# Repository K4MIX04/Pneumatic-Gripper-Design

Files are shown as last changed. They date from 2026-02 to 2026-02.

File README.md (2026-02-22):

# Pneumatic Gripper Design (University Project)

This repository contains an academic project completed as part of my Automation and Robotics degree at AGH University of Science and Technology.

## Project Overview
The goal of the assignment was to design a functional pneumatic gripper capable of lifting a specific payload, starting from basic kinematic equations up to a complete 3D assembly and technical documentation.

### Key phases of the project:
* **Kinematic & Force Analysis:** Mathematical calculations and simulations (using SAM) to determine the required gripping forces and stroke lengths.
* **Component Selection:** Sizing and selecting an appropriate pneumatic cylinder from the industrial **Festo** catalog.
* **CAD Modeling & FEA:** 3D parametric modeling and stress analysis (von Mises) performed in **Autodesk Inventor** to verify structural integrity.
* **Technical Documentation:** Creation of 2D assembly drawings and a complete Bill of Materials (BOM).

---

### Project Gallery

**
**Fig 1.** 3D Render of the designed gripper.

**
**Fig 2.** Finite Element Analysis (FEA) / von Mises stress test in Autodesk Inventor.

**
**
**Fig 3.** 2D Assembly Drawing.

---
*Note: This is strictly an educational project created for university coursework. Full documentation (in Polish) is available in the attached PDF file.*

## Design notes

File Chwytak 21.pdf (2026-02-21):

1

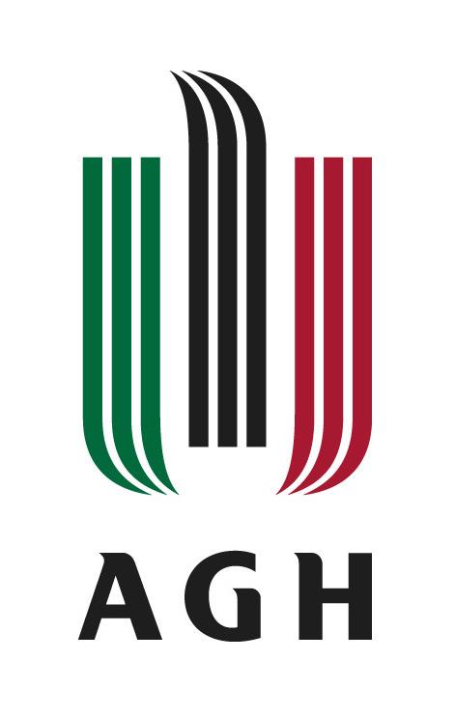
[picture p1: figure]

Projekt konstrukcyjny chwytaka nr 21 typu P – (O – P – Os)

## Projekt konstrukcyjny chwytaka nr 21 typu P – (O – P – Os)

Prototypowanie konstrukcji w technice druku 3D i CNC

## Kamil Górak

## Automatyka i Robotyka Wydział Elektrotechniki, Automatyki, Informatyki i Inżynierii Biomedycznej

2

## Spis treści

1. Założenia wykonywanego projektu | 3
2. Schemat chwytaka przemysłowego | 3
3. Obliczenia ruchliwości zadanego chwytaka | 3
4. Wyznaczenie maksymalnej siły ciężkości wałka | 4
5. Wyznaczanie potrzebnej siły chwytu | 4
6. Wyznaczenie minimalnej długości szczęk | 5
7. Wyznaczenie długości poszczególnych elementów chwytaka | 5
8. Charakterystyka przesunięciowa | 7
9. Charakterystyka prędkościowa | 10
10. Charakterystyka siłowa | 11
11. Wytrzymałość na ścinanie dla sworznia | 14
12. Analiza wytrzymałościowa w programie Autodesk Inventor | 15
13. Dobór siłownika | 16
14. Rysunek złożeniowy chwytaka | 17
15. Źródła | 20

3

## 1. Założenia wykonywanego projektu

- Obiektem przeznaczonym do przeniesienia jest wałek o średnicy zewnętrznej wynoszącej 80 mm, długości 140 mm, wykonany ze stopu aluminium
- Urządzenie ma za zadanie chwycić transportowany element, utrzymać go podczas transportu i uwolnić w miejscu docelowym
- Siłownik chwytaka jest zasilany sprężonym powietrzem o ciśnieniu 0,6 MPa

## 2. Schemat chwytaka przemysłowego

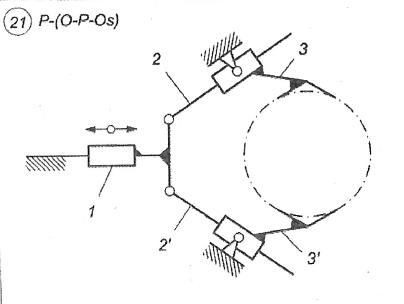
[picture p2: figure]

## 3. Obliczanie ruchliwości zadanego chwytaka

Aby wyznaczyć ile elementów jest potrzebne do napędu projektowanego urządzenia posługuję się następującym wzorem:
W = 3n - ∑ ( i − 3)

5
i=3 | pin
Który po przekształceniu do obecnych warunków zadania przyjmuje postać: W = 3n – p4 - 2p5
Gdzie:
W – ruchliwość chwytaka
n – liczba członów ruchomych
p4 – liczba par kinematycznych klasy czwartej p5 – liczba par kinematycznych klasy piątej

4

Po podstawieniu wartości:
n = 5
p4 = 0
p5 = 7
W = 3*5 – 0 – 2*7 = 1

Z faktu, że W = 1 wynika, że do napędu chwytaka wymagany jest jeden siłownik o ruchu liniowym

## 4. Wyznaczanie maksymalnej siły ciężkości wałka

Maksymalny ciężar transportowanego elementu uzyskuję ze wzoru:
Qmax = πr
2

lρg
Gdzie:
r = 40 mm promień wałka
l = 140 mm długość wałka
ρ = 2700 kg m3 | przyjęta gęstość aluminium
| Qmax = 3,1415 * (0,04m)² * 0,14m * 9,81m
s2

* 2700 kg
m3
Qmax = 18,64N

## 5. Wyznaczanie potrzebnej siły chwytu

Ustalenie wymaganej siły chwytu przebiega na podstawie analizy poniższego schematu przedstawiającego szczęki zaciśnięte na przedmiocie

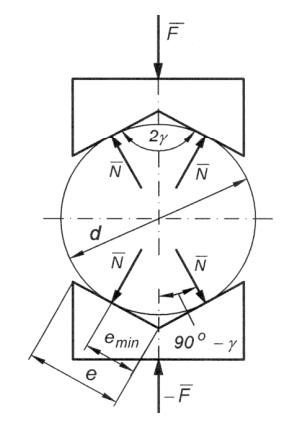
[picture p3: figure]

5

Przyjmujemy następujące wartości: μ = 0,3
2γ = 125o
n = 2
Qmax = 18,64 N
Na podstawie powyższego schematu oraz podanych wartości przystępujemy do wyznaczenia potrzebnej siły chwytu
Fch = 2 N cos(90o – γ) | → | N = Fcℎ
2sinγ
T = μ n | → | T = μFch
2sinγ
Aby udało się chwycić wałek musi być spełniony następujący warunek
4T ≥ Qn | → | Fch ≥

nQmaxsinγ
2μ
Podstawiając wartości liczbowe otrzymuję
Fch ≥ 82,67N

## 6. Wyznaczenie minimalnej długości szczęk

Korzystając ze schematu przedstawionego w poprzednim punkcie przystępuję do wyznaczenia długości szczęk korzystając z zależności:
tg γ =

0,5d
emin

→ emin =

d
2tgγ

≈ 21 mm
Aby mieć pewność, że wyznaczona długość będzie wystarczająca przyjmuję e z określonego zakresu
e = (1,1 – 1,5) emin
W związku z powyższym w moim przypadku e = 30 mm

## 7. Wyznaczenie długości poszczególnych elementów chwytaka

Aby wyznaczyć odpowiednie długości poszczególnych części chwytaka a także kątów między nimi użyłem programu Autodesk Inventor. Zaprojektowałem w nim schemat kinematyczny wykonywanego manipulatora uzyskany poprzez łączenie odpowiednich ramion wiązaniami, ustalanie stałych długości. Wykonywane czynności tj. zmiana poszczególnych wartości pozwoliły mi wyznaczyć wymiary, przy których chwytak pracował w zadowalający sposób. Używany schemat a także wyznaczone z niego długości, które będą wykorzystywane w dalszym ciągu obliczeń umieściłem poniżej.

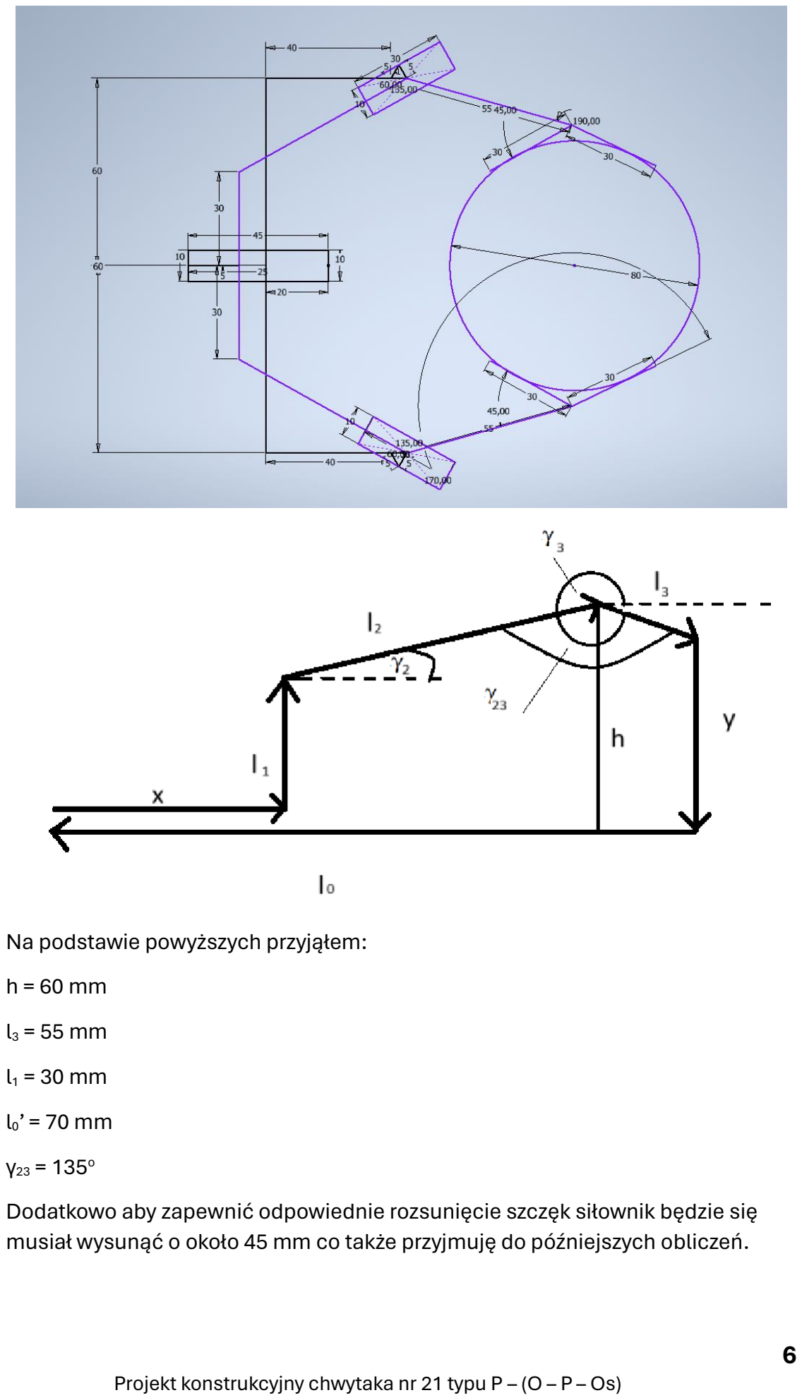
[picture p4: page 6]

6

Na podstawie powyższych przyjąłem: h = 60 mm
l3 = 55 mm
l1 = 30 mm
l0’ = 70 mm
γ23 = 135o
Dodatkowo aby zapewnić odpowiednie rozsunięcie szczęk siłownik będzie się musiał wysunąć o około 45 mm co także przyjmuję do późniejszych obliczeń.

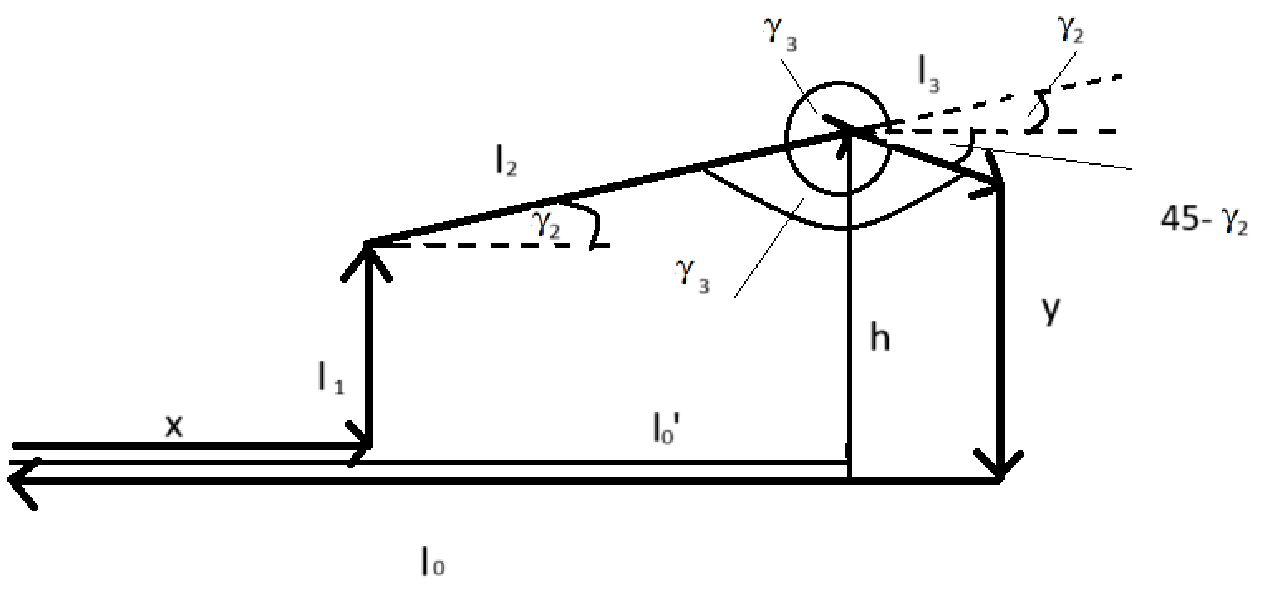
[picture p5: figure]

7

## 8. Charakterystyka przesunięciowa

Aby wyznaczyć funkcję położenia szczęki w zależności od wysunięcia tłoka posługuję się schematem z powyższego punktu uzupełnionym o dodatkową odległość i kąty.

Korzystając z metody wieloboku wektorowego zamkniętego przystępuję do wyznaczania charakterystyki przesunięciowej.

Zapisuję równania wektorowe dla dwóch wieloboków, które mogę wyróżnić
x̅+ l̅1 + l̅2 + l̅3 + y̅ + l̅0 = 0 x̅+ l̅1 + l̅2 + ℎ̅ + l′0

̅̅ = 0

Następnie zapisuję równania dla obu osi dla wieloboku mniejszego x + l2cos γ2 - l0’ = 0
l1 + l2sin γ2 - h = 0
l0’ – x = l2cos γ2
h – l = l2cos γ2
(l0’ – x)² = l2

2cos² γ2
(h – l1)

2 = l2

2sin² γ2
(l0’ – x)² + (h – l1)

2 = l2
2

(cos² γ2 + sin² γ2)
l2 = √(l0’ – x)
2 + (h – l1)

2
cos γ2 =

l

′0−x

l2

=

l

′0−x
√(l0’ – x)² + (h – l1)²
sin γ2 =

ℎ−l1
l2

=

ℎ−l1
√(l0’ – x)² + (h – l1)²

Dodatkowo zauważam, że
γ3 = 315o + γ2

8

Wyznaczone z małego wieloboku dane używam do rozwiązania układu większego wieloboku.
x + l2cos γ2 + l3cos γ3 - l0 = 0 l1 + l2sin γ2 + l3sin γ3 - y = 0 x + l1 + l2(

l

′0−x

l2

+

ℎ−l1
l2

) + l3(cos γ3 + sin γ3) – l0 - y = 0 h + l’0 + l3(cos γ3 + sin γ3) – l0 – y = 0

Dodaję kolejne równanie odczytane ze schematu: l0 = l’0 + l3cos(45o

- γ2)
Wracając do wcześniejszego równania:
h + l’0 + l3(cos(315o + γ2) + sin (315o + γ2)) -l3cos(45o
- γ2) – y – l’0 = 0

h + l3[(√2
2

l

′0−x
√(l0’ – x)² + (h – l1)² +

√2
2

ℎ−l1
√(l0’ – x)² + (h – l1)²

) + (−

√2
2

l

′0−x
√(l0’ – x)² + (h – l1)² +

√2
2

ℎ−l1
√(l0’ – x)² + (h – l1)²

) - (

√2
2

l

′0−x
√(l0’ – x)² + (h – l1)² +

√2
2

ℎ−l1
√(l0’ – x)² + (h – l1)²

)] = y

Po uproszczeniu dochodzę do równania y = h + l3

√2
2

(

x+ℎ−l1−l′0
√(l0’ – x)² + (h – l1)²

)

Po podstawieniu wartości liczbowych otrzymuję charakterystykę przesunięciową: y = 60 + 27,5√2 (

x−40
√(70−x)2+900

)

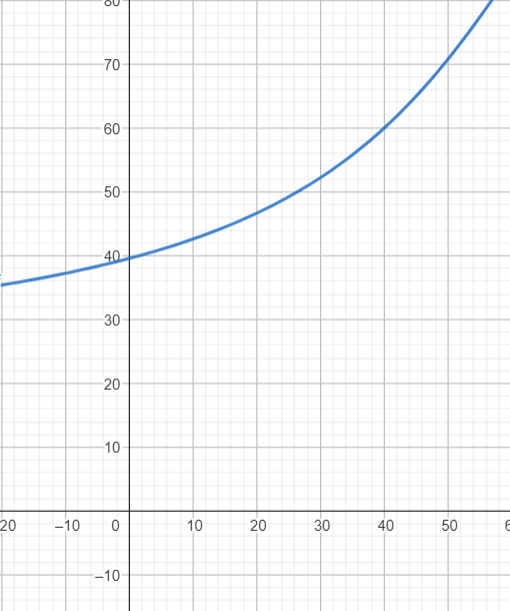
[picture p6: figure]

Przedstawiony powyżej wykres został wygenerowany przez stronę geogebra.org i przedstawia wykres charakterystyki według wyznaczonego równania. Uzyskana

9

charakterystyka jest zgodna ze schematem wykonanym w Autodesk Inventor tzn. wysunięcie tłoka o daną długość i zmiana wysokości y są zgodne ze sobą. Aby jeszcze dokładniej przekonać się o poprawności wyznaczonej charakterystyki zamodelowałem schemat chwytaka w programie SAM 8.3, który zamieściłem poniżej.

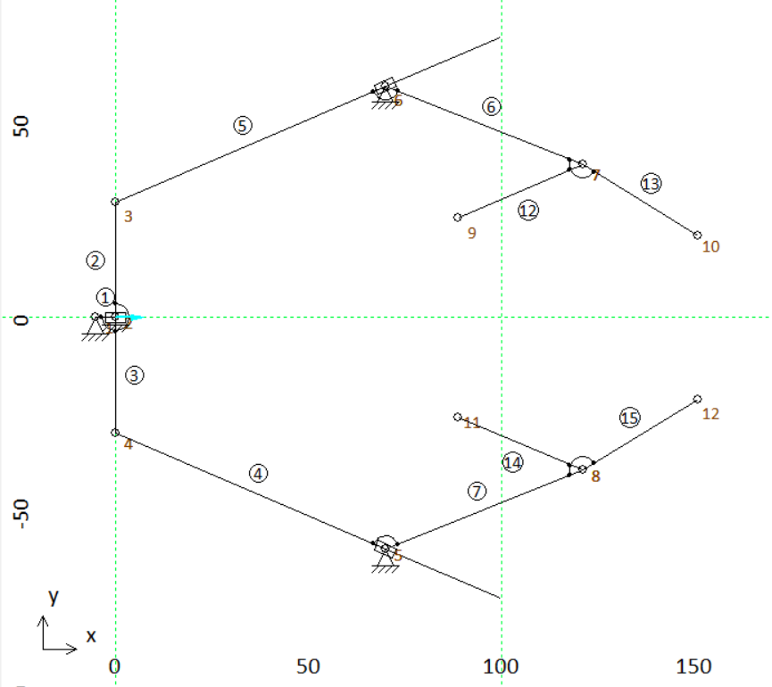
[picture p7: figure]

Wykorzystując wbudowaną w program funkcję do generowania wybranych wykresów otrzymałem następującą charakterystykę przesunięciową.

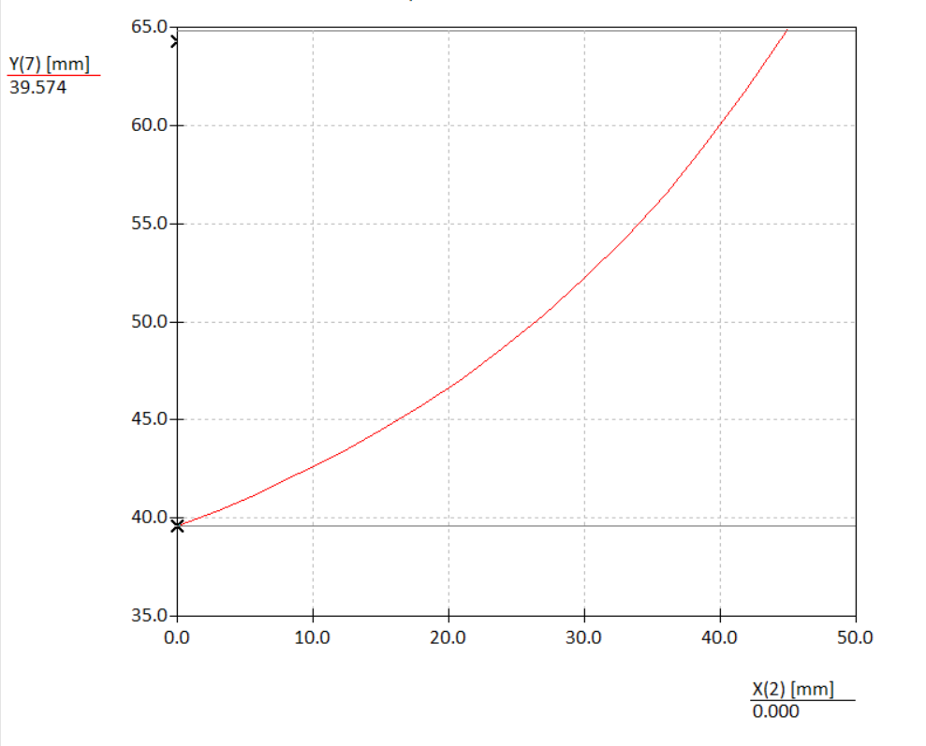
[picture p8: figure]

Powyższy wykres dokładnie nakłada się na wykres uzyskany z własnoręcznych obliczeń.

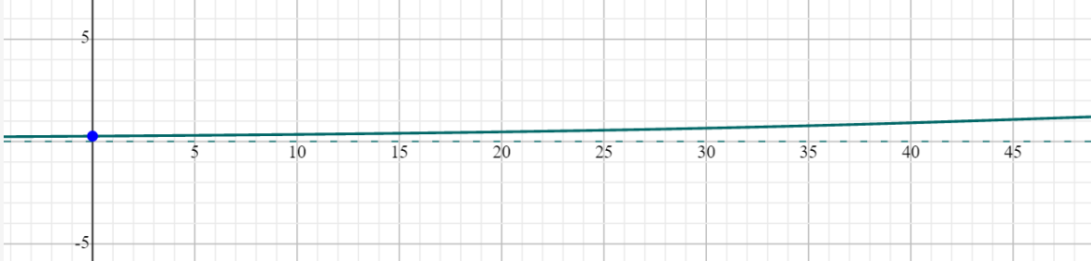
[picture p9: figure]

10

## 9. Charakterystyka prędkościowa

Charakterystykę prędkościową wyliczam metodą analityczną licząc pochodną y(x) po zmiennej x.

d
dx

y =

d
dx

(60 + 27,5√2 (

x−40
√(70−x)²+900

))

Otrzymuję:

fv (x) = | −825√2x+82500√2

x

| 2∗√(70−x)2+900−140x√(70−x)2+900+5800√(70−x)2+900
Generuję wykres z użyciem programu symbolab.com

Sprawdzam czy otrzymałem dobrą charakterystyką porównując otrzymany powyżej wykres z wygenerowanym przez program SAM

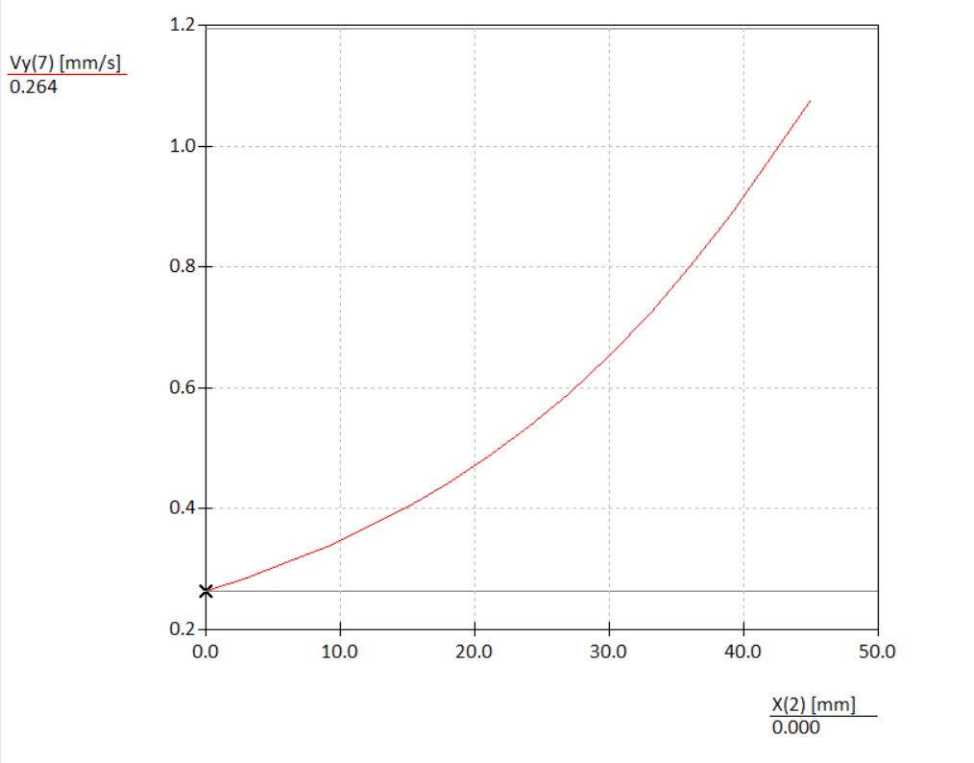
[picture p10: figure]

Porównując wybrane wartości mogę stwierdzić, że wykresy te są ze sobą zgodne.

11

## 10. Charakterystyka siłowa

Pierwszym sposobem wyznaczenia charakterystyki siłowej jest metoda analityczna, która polega na rozpatrywaniu sił działających na poszczególne części członów.
a) Człon 1

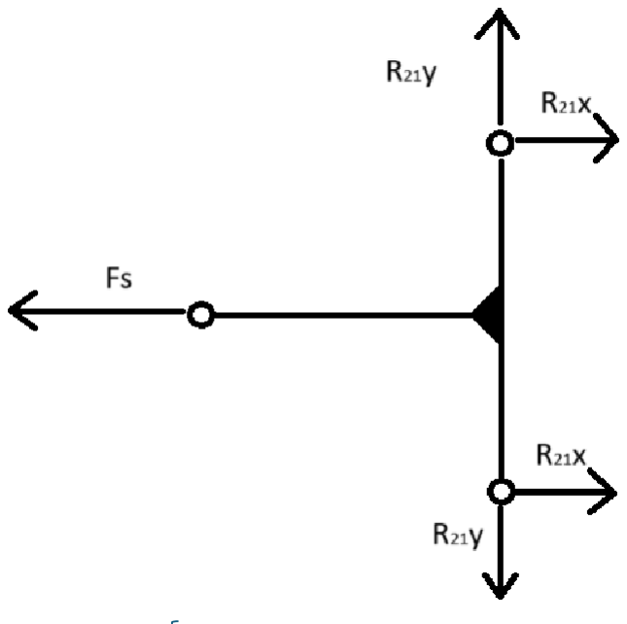
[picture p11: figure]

-FS + 2R21

x = 0
FS = 2R21
x
b) Człon 2

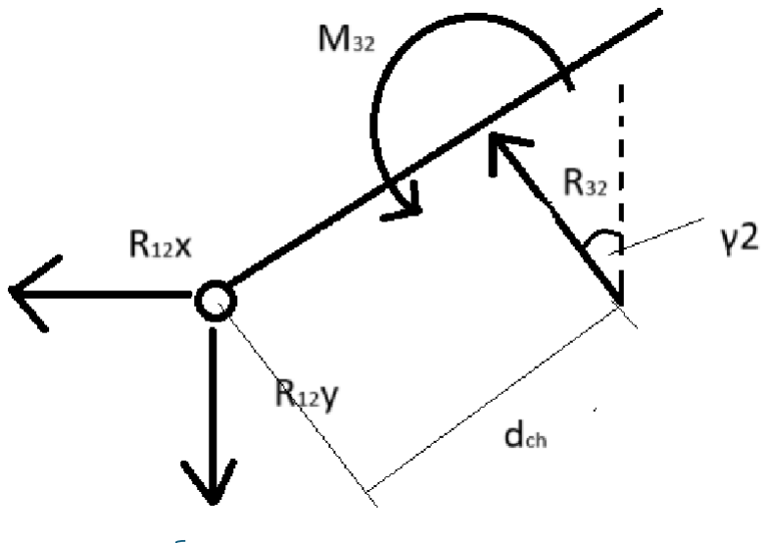
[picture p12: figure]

- R12

X – R32*sin γ2 = 0
- R12

y + R32*cos γ2 = 0
M32 – R32*dch = 0
c) Człon 3

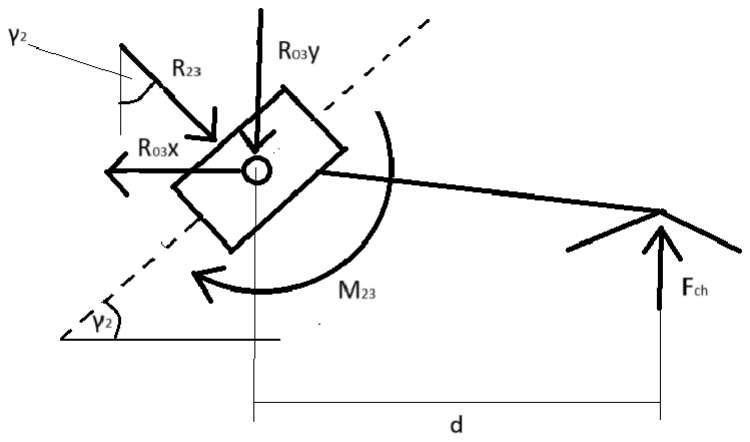
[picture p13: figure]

12

- R03

X + R23*sin γ2 = 0
-R03

Y – R23cos γ2 + Fch = 0
- M23 + Fch*d = 0

Podsumowując wszystkie otrzymane równanie otrzymujemy:
- FS + 2R21

x = 0
FS = 2R21
x
- R12

X – R32*sin γ2 = 0
- R12

y + R32*cos γ2 = 0
M32 – R32*dch = 0
- R03

X + R23*sin γ2 = 0
-R03

Y – R23cos γ2 + Fch = 0
- M23 + Fch*d = 0
Wykorzystując znane wartości: γ2 = 29,2o
d = 52,923 mm
dch = 61,483 mm
Fch = 82,67 N
Otrzymujemy równania, z których wyznaczamy kolejno: M23 = Fch * d
M23 = 82,67 N * 0,052923 m = 4,375 Nm R32 =

M32
dcℎ

= 71,158 N

R12

y = R32cos γ2 = 62,115 N

R12

x = - R32sin γ2 = - 34,715 N

Fs = 2R21

x = 69,43 N
Wyznaczona powyżej siła to minimalna siła jaką musi posiadać siłownik aby zacisnąć szczęki z minimalną wymaganą siłą, tak aby wałek się nie wyślizgnął.

Aby sprawdzić poprawność wyznaczonej siły skorzystam z metody mocy chwilowych. Korzystając ze wzoru:
Fcℎ
Fs =

1
2fv(x)

Który po przekształceniu i podstawieniu wartości przyjmuje postać:

2 ∗

−825√2x + 82500√2

x

2 ∗ √(70 − x)

2 + 900 − 140x√(70 − x)

2 + 900 + 5800√(70 − x)
2 + 900

∗ 82,67

Korzystając z Geogebry generuję wykres powyższej funkcji

13

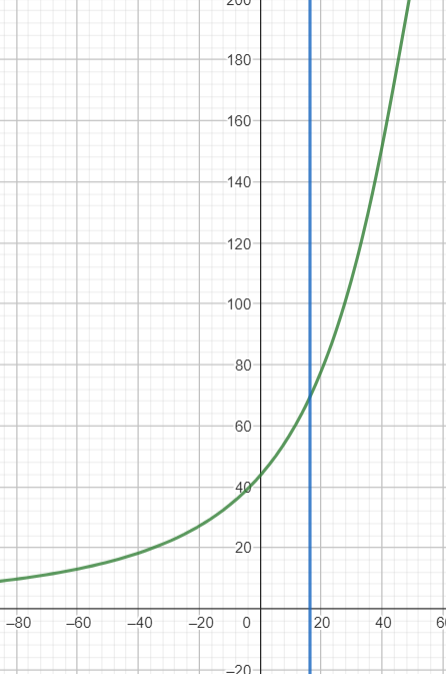
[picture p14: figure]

Aby się upewnić skorzystałem również z opcji oferowanych przez program SAM, który po przyłożeniu siły w sposób przedstawiony poniżej pozwala wygenerować wykres siły potrzebnej na tłoku.

Zielonym kolorem został
oznaczony szukany wykres a pionowa niebieska kreska
symbolizuje punkt, w którym szczęki zaciskają się na wałku. Siła w tym miejscu wynosi w
zaokrągleniu 70 N co zgadza się z wyznaczeniem metodą
analityczną

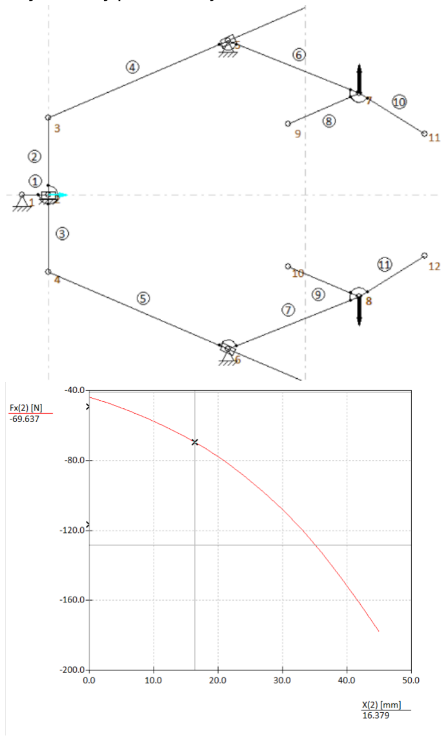
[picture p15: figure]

14

Zaznaczony punkt symbolizuje miejsce, w którym szczęki się zaciskają co po raz kolejny potwierdza poprawność wykonanych obliczeń.

## 11. Wytrzymałość na ścinanie dla sworznia

Po analizie schematu chwytaka stwierdzam, że największym obciążeniom będzie podlegał sworzeń znajdujący się na belce, do której przymocowany jest tłok, gdyż będzie on pojedynczy w przeciwieństwie do sworznia mocującego ramę ze szczękami, który będzie łączony za pomocą dwóch sworzni z każdej strony jeden.

Warunek wytrzymałości sworznia na ścinanie jest wyrażony zależnością:
στ≤ kτ, gdzie
kτ – dopuszczalne naprężenie ścinające
στ – maksymalne naprężenie ścinające

kτ = 132 MPa (odczytane z dostępnych źródeł)

στ =

2T
π∗d²
d – średnica sworznia (przyjęta) = 6 mm
T – siła tnąca
Korzystając z przeprowadzonej wcześniej analizy siłowej mogę obliczyć siłę ścinającą działającą na wybrany sworzeń. (Punkt 10, podpunkt b)

T = √(R03y)
2 + (R03x)

2

T = √(62,115N)
2 + (34,715N)

2
T = 71,16 N
Co podstawiam do wyżej zapisanych wzorów i otrzymuję:

στ =

2∗71,16N
3,1415∗(0,006m)²

= 1,26 MPa

Otrzymane wyniki prowadzą do stwierdzenia, że sworzeń wytrzyma działanie na niego sił ścinających.

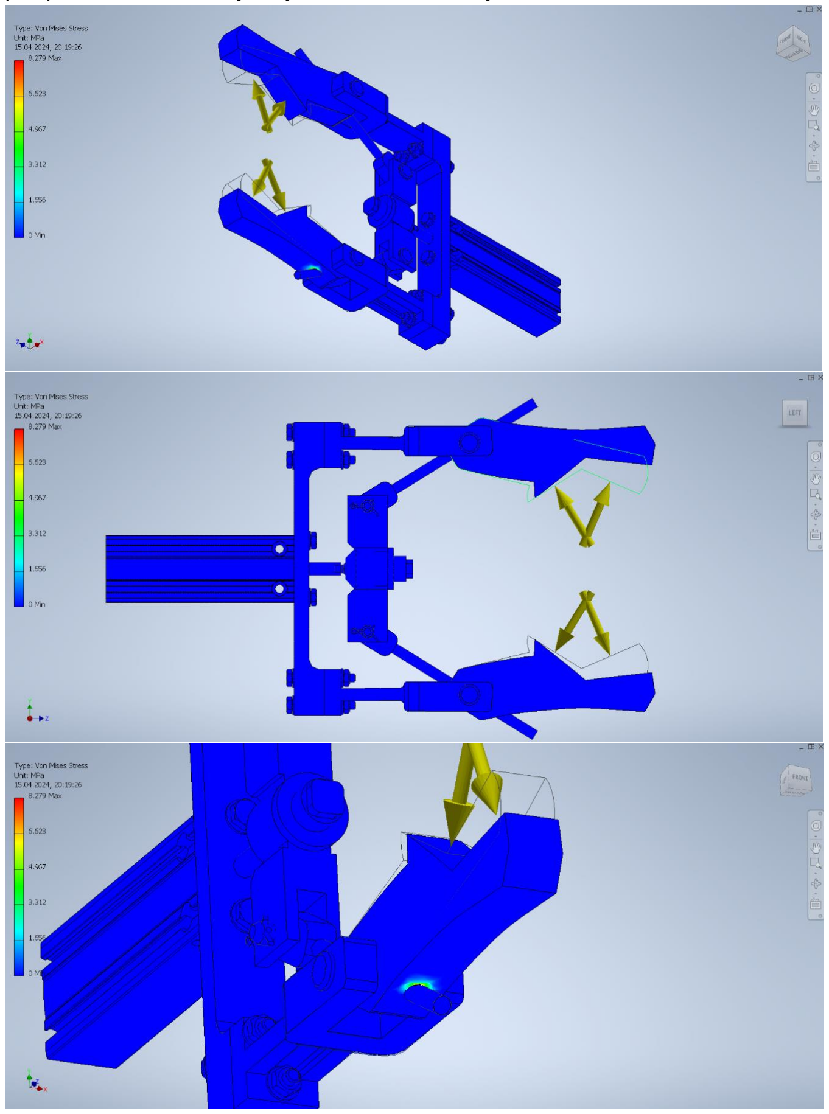
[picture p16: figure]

15

## 12. Analiza wytrzymałościowa w programie Autodesk Inventor

Aby sprawdzić czy chwytak wytrzyma poddawane mu obciążenia i działające siły przeprowadziłem analizę z użyciem modułu Analizy w Inventorze.

Wyniki potwierdzają, że chwytak wytrzyma obciążenia.

16

## 13. Dobór siłownika

Z analizy siłowej wiadomo, że siła siłownika musi wynosić co najmniej 69,43 N

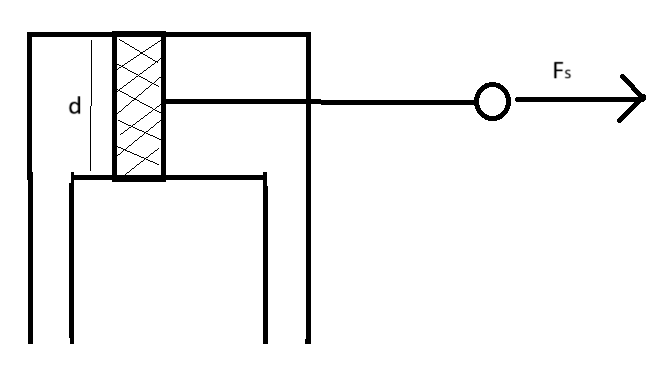
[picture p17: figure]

Obliczyć należy również średnicę siłownika czego dokonuję z poniższego wzoru: Fs =

π∗d

2

4

* pn
Gdzie pn to ciśnienie zasilające, które wynosi 0,6 MPa d ≥ √
4Fs
πpn
Po podstawieniu wartości otrzymuję: d ≥ 12,2 mm

Po uwzględnieniu wszystkich wymaganych wartości wybrałem siłownik 4833192 DPDM-16-50-PA z katalogu firmy Festo, którego charakterystykę zamieściłem na następnej stronie.

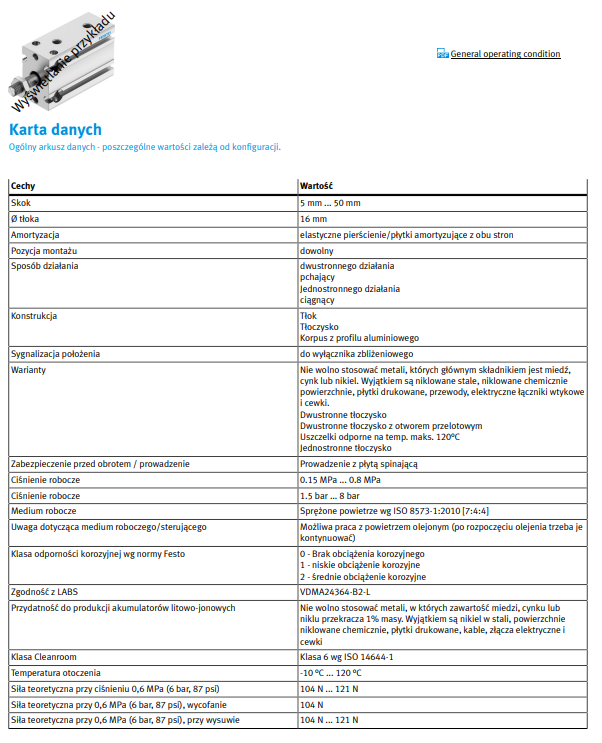
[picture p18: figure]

17

## 14. Rysunek złożeniowy chwytaka

Po dokonaniu wszystkich niezbędnych obliczeń, doborze odpowiedniej długości elementów i wybraniu odpowiedniego do wykonywanego zadania siłownika przystąpiłem do projektowania urządzenia, którego rysunek złożeniowy zamieściłem poniżej.

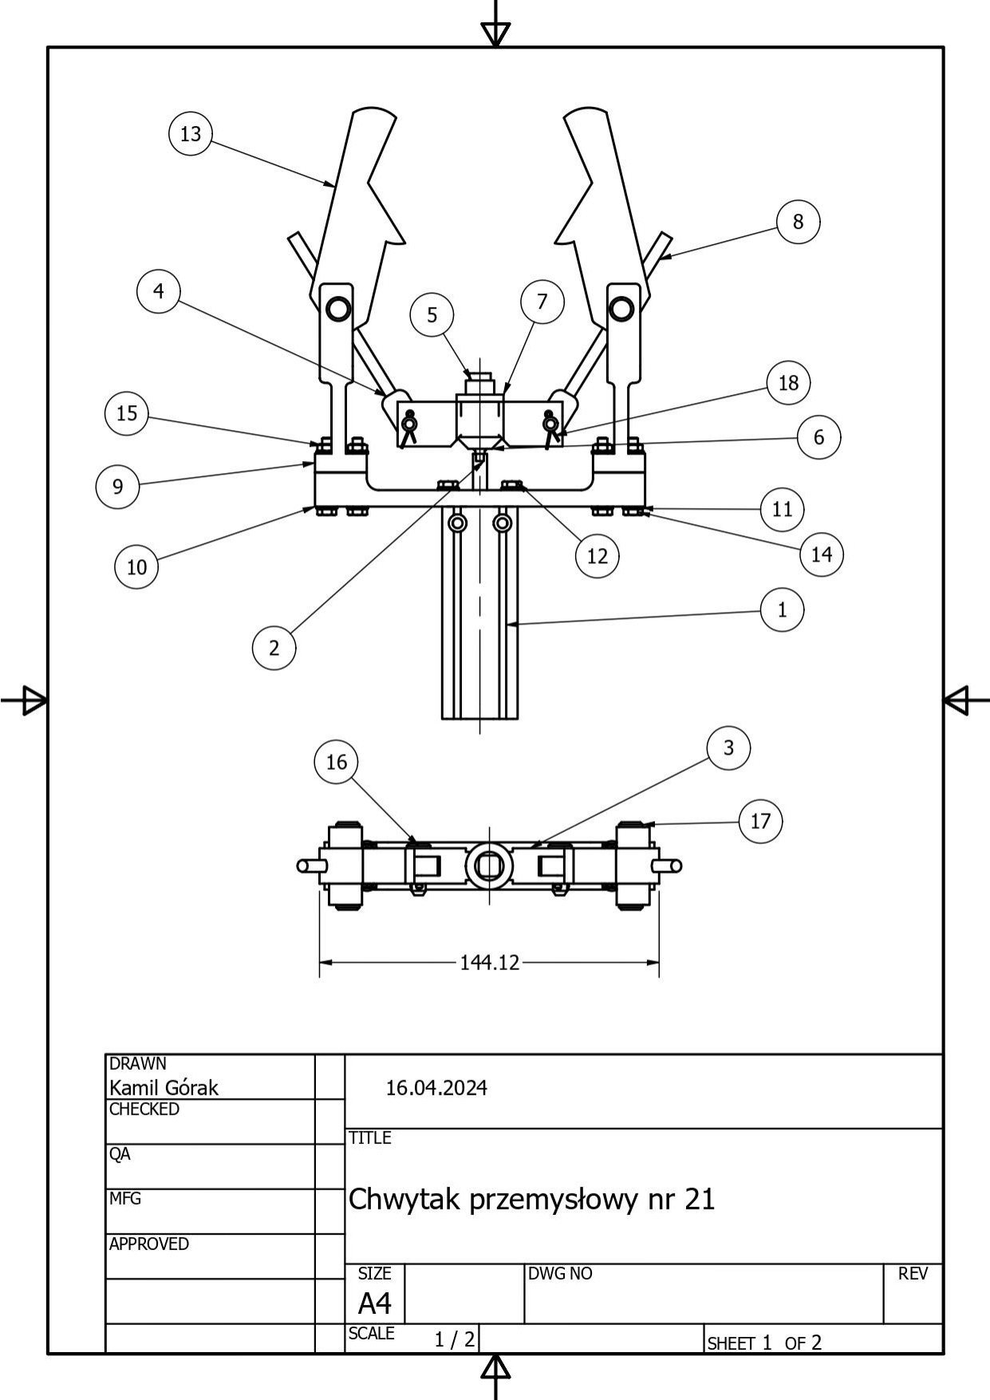
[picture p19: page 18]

18
Projekt konstrukcyjny chwytaka nr 21 typu P

– (O

– P

– Os)

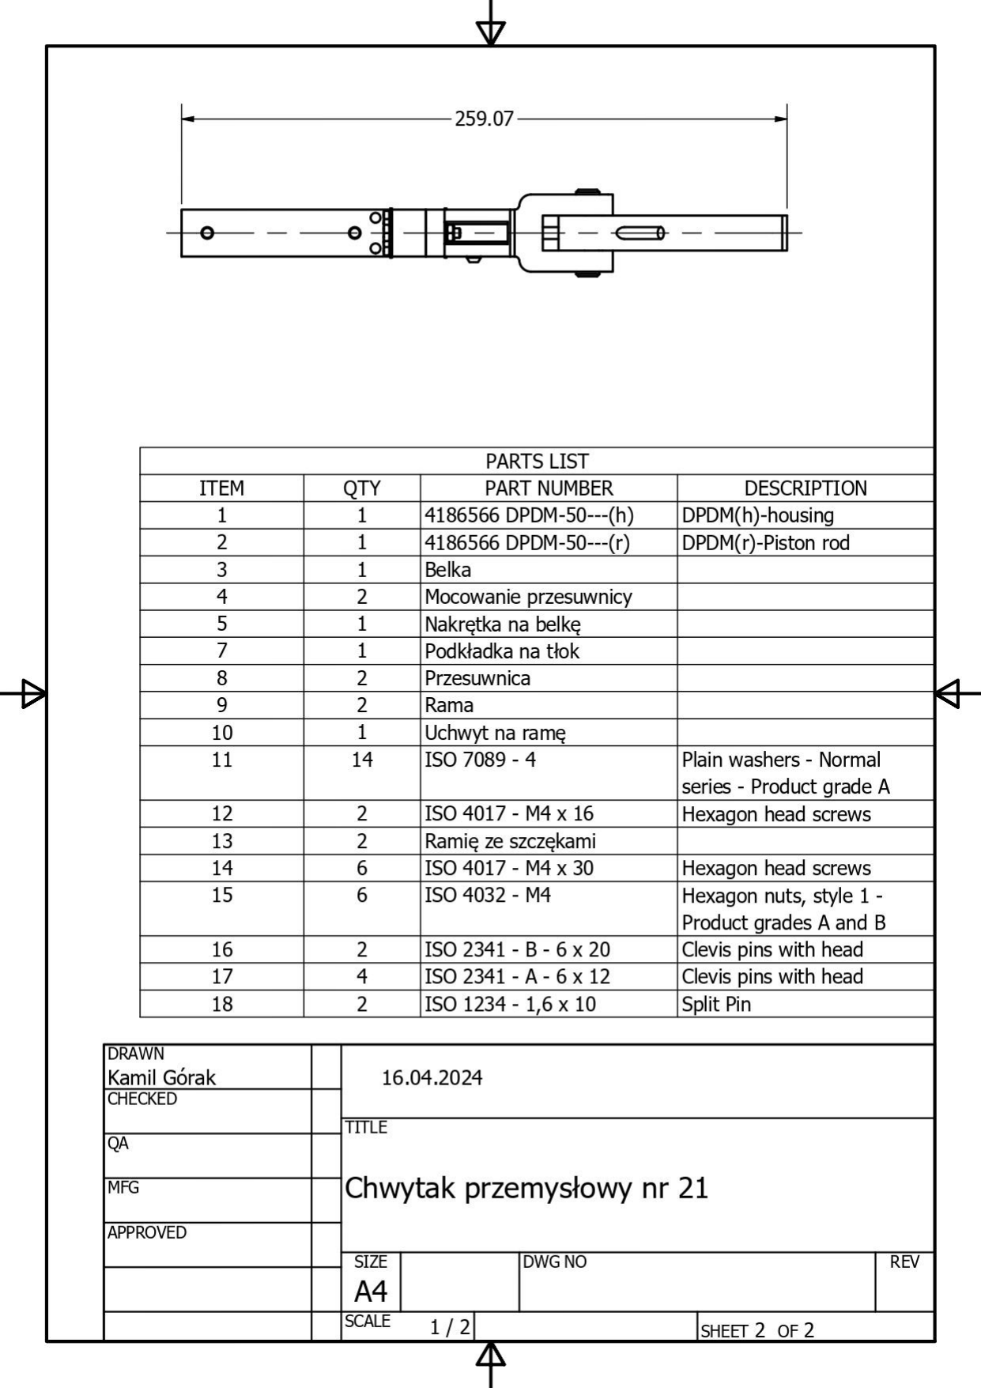
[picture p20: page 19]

19
Projekt konstrukcyjny chwytaka nr 21 typu P

– (O

– P

– Os)

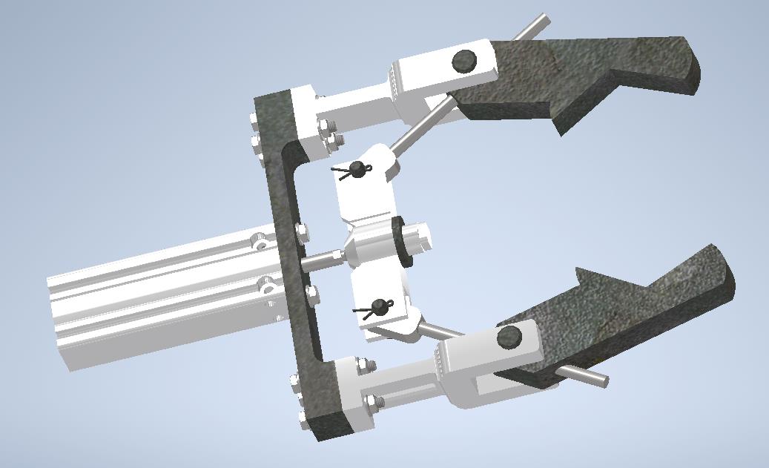
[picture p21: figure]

20

## 15. Źródła

- https://www.festo.com/pl/pl/
- https://www.symbolab.com
- https://www.geogebra.org/calculator
- https://www.artas.nl/en/

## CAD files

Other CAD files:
Złożenie testowe.dwg
4186566 DPDM-50---(r).ipt
Belka.ipt
Mocowanie suwaka.ipt
Nakrętka na belkę.ipt
Nakrętka na tłok.ipt
Podkładka na tłok.ipt
Rama.ipt
Ramię ze szczękami.ipt
Siłownik.ipt
Suwak.ipt
Uchwyt na ramę.ipt
Wałek.ipt
Złożenie testowe.iam

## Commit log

2026-02-21 add gripper design pdf
2026-02-23 stl files upload
    [4186566 DPDM-50---(r).ipt, Belka.ipt, Mocowanie suwaka.ipt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]
